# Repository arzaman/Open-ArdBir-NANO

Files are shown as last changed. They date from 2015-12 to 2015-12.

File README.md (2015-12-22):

# Open-ArdBir-NANO
Repository for HW design file (PCB, schematic)  of ArdBir board based on arduino NANO version

Open Ardbir is an open source SW (up to release 2.8.3) to control and automate beer brewing process
The SW have been developed based on Arduino UNO board (Atmega328 MCU) with few surroundings HW component to drive and interface external element (PUMP, Heating element , LCD, push button etc.)

There are few open source HW board available supporting the SW either designed as  shield on top of Arduino Board or stand alone board (all in one board)

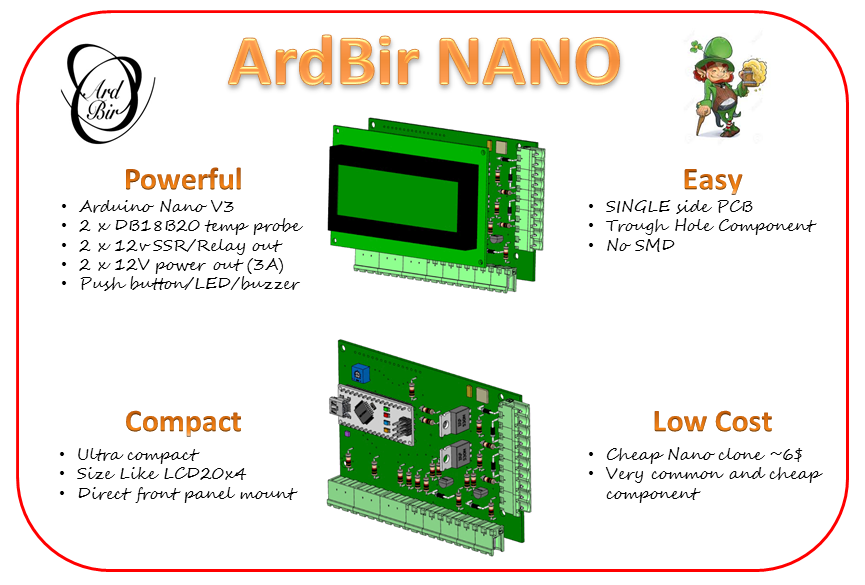
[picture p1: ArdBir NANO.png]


In the repository you can find my personal design of a board based on Arduino NANO V3 version with few additional features (not all supported by current SW version)

•	2 x DB18B20 temp probe

•	2 x 12v SSR/Relay out

•	2 x 12V power out (3A) 

•	Push button/LED/buzzer

The mapping of pinout is completely compatible with all other version (1 x DS18B20,SSR,PUM) while the second set of input is for future applications
The 12V power output can drive directly small pump (like solar project) and/or solenoid valve

The board has been designed in a very compact size to be mounted front panel

•	double side PCB

•	Trough Hole Component

•	No SMD

Two version of PCB are available depending on the LCD mounting

•	LCD solder side: the LCD is mounted on the copper side leaving the components accessible

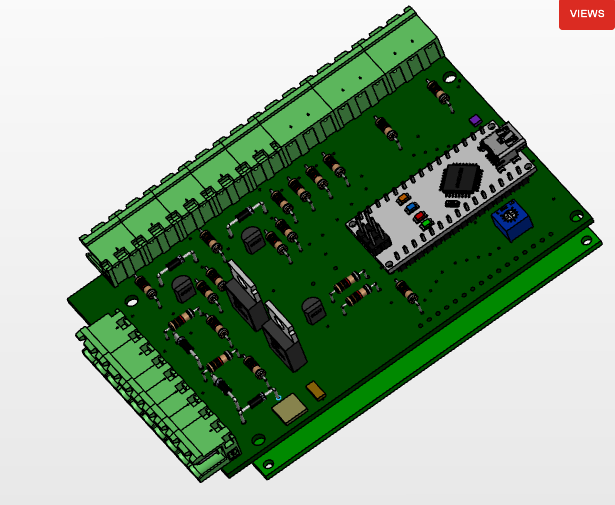
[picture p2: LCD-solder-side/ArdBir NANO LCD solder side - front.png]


•	LCD on component side : LCD is mounted on the same side of components 

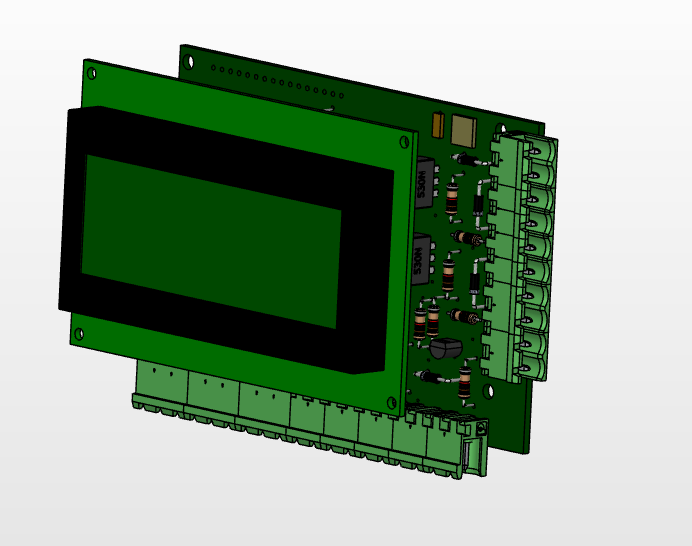
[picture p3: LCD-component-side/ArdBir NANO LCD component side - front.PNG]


In the repository you can find two folders, one for each version, containing PCB and schematic in eagle forma and BoM

![Alt text] (https://github.com/arzaman/Open-ArdBir-NANO/blob/master/LCD-solder-side/ArdBir%20NANO%20schematic.png)

Enjoy and feel free to modify/fork the project

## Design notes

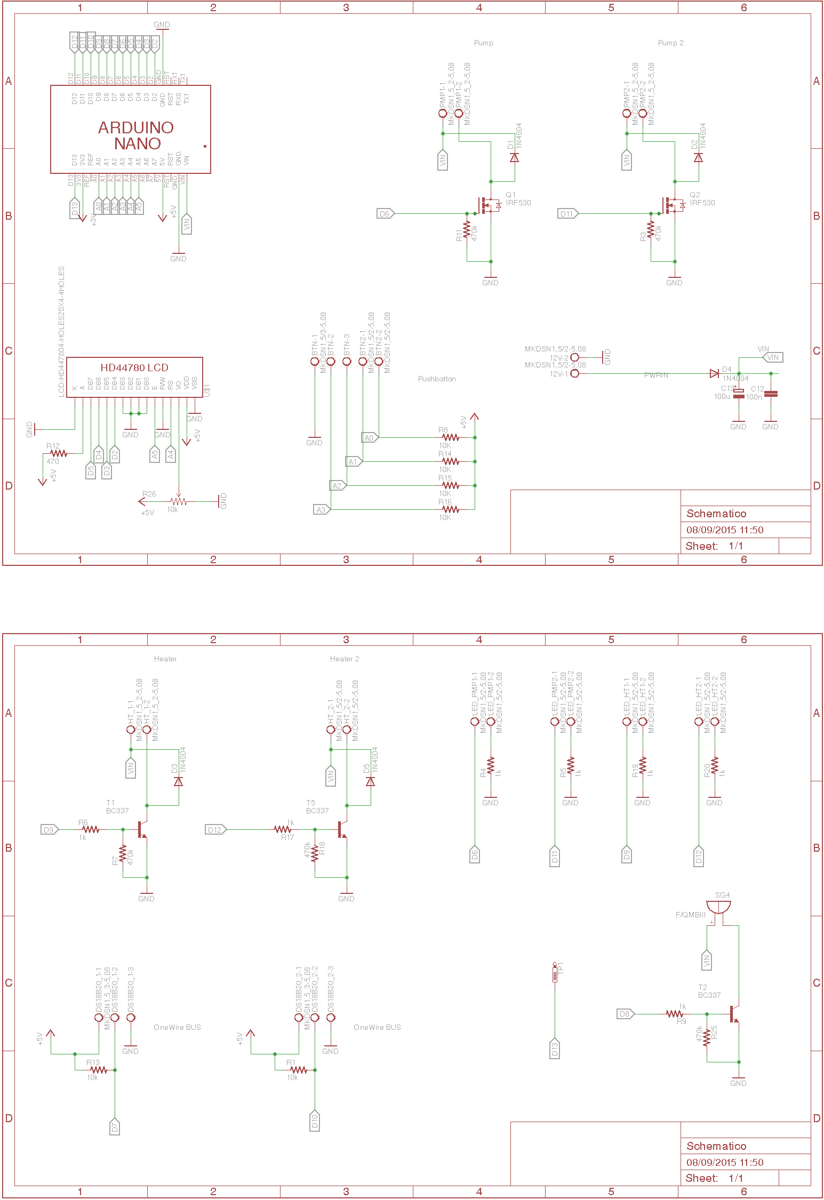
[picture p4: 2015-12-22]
LCD-component-side/ArdBir NANO schematic.png

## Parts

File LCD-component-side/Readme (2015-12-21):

file for the PCB with LCD mounted component side

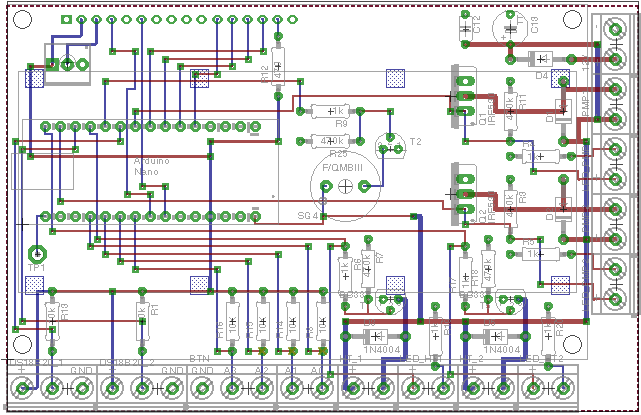
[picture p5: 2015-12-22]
LCD-component-side/ArdBir NANO PCB.png

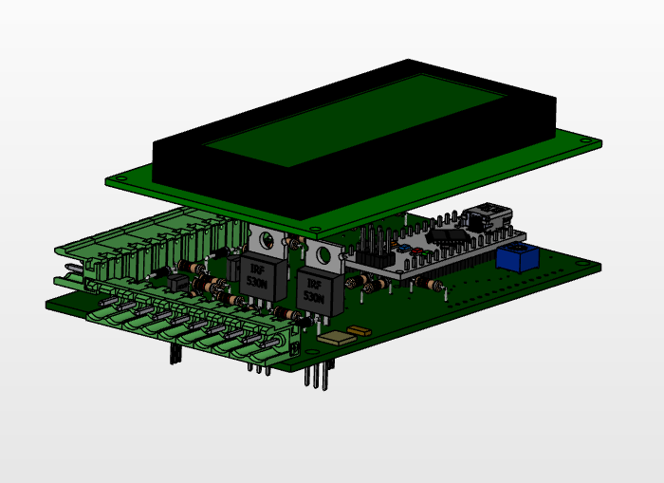
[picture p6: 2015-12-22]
LCD-component-side/ArdBir NANO LCD component side - mid.PNG

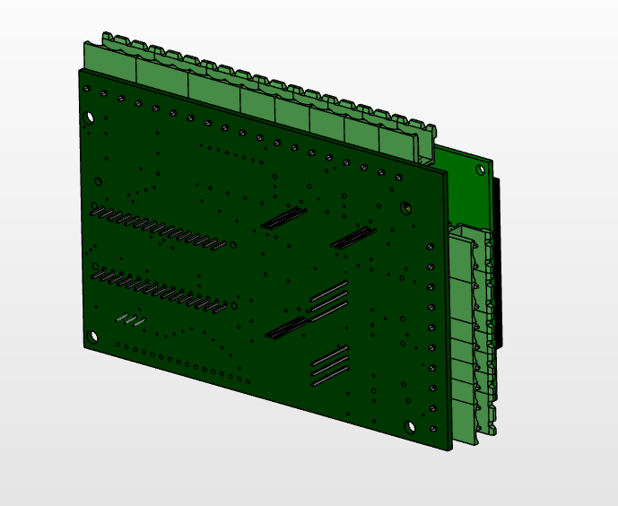
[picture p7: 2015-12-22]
LCD-component-side/ArdBir NANO LCD component side - back.PNG

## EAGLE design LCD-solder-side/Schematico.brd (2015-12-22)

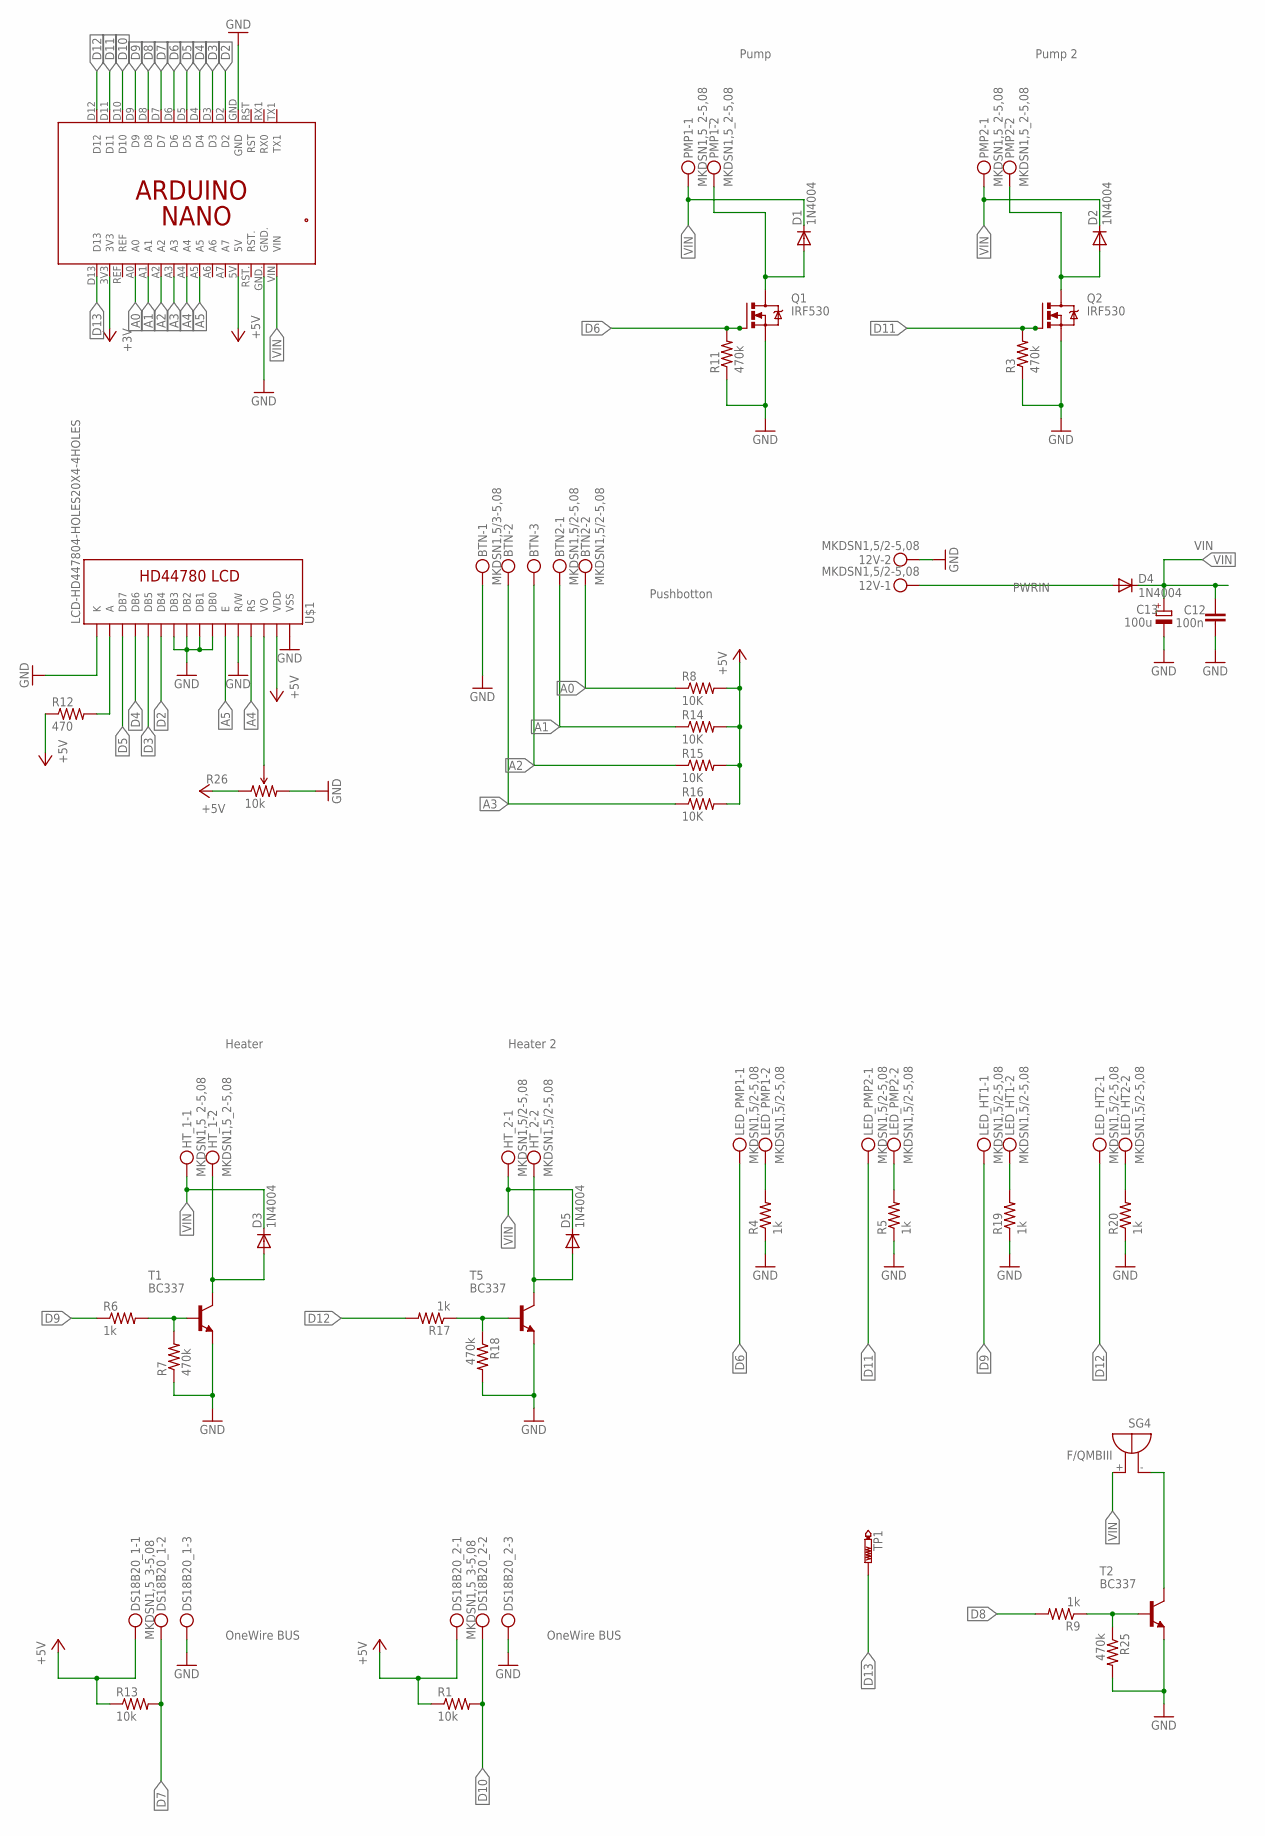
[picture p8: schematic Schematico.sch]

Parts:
12V: MKDSN1,5/2-5,08
BTN: MKDSN1,5/3-5,08
BTN2: MKDSN1,5/2-5,08
C12: 100n; C050-024X044
C13: 100u; TT5D6
D1, D2, D3, D4, D5: 1N4004; DO41-10
DS18B20_1, DS18B20_2: MKDSN1,5_3-5,08; MKDSN1,5-3-5,08
HT_1: MKDSN1,5_2-5,08; MKDSN1,5-2-5,08
HT_2: MKDSN1,5/2-5,08
LED_HT1, LED_HT2: MKDSN1,5/2-5,08
LED_PMP1, LED_PMP2: MKDSN1,5/2-5,08
PCB1: ARDUINO_NANO
PMP1, PMP2: MKDSN1,5_2-5,08; MKDSN1,5-2-5,08
Q1, Q2: IRF530; TO220BV
R1, R13: 10k; 0207/10
R3, R7, R11, R18, R25: 470k; 0207/10
R4, R5, R6, R9, R17, R19, R20: 1k; 0207/10
R8, R14, R15, R16: 10K; 0207/10
R12: 470; 0207/10
R26: 10k; 3362U-2
SG4: F/QMBIII
T1, T2, T5: BC337; TO92
TP1: PTR1PAD1-20; P1-20
U$1: LCD-HD447804-HOLES20X4-4HOLES; LCD-20X4-4HOLES

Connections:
+3V: PCB1.3V3
+5V: DS18B20_1.1, DS18B20_2.1, PCB1.5V, R1.1, R8.2, R12.1, R13.1, R14.2, R15.2, R16.2, R26.1 (CCW), U$1.P$2 (VDD)
A0: BTN2.2, PCB1.A0, R8.1
A1: BTN2.1, PCB1.A1, R14.1
A2: BTN.3, PCB1.A2, R15.1
A3: BTN.2, PCB1.A3, R16.1
A4: PCB1.A4, U$1.P$4 (RS)
A5: PCB1.A5, U$1.P$6 (E)
D2: PCB1.D2, U$1.P$11 (DB4)
D3: PCB1.D3, U$1.P$12 (DB5)
D4: PCB1.D4, U$1.P$13 (DB6)
D5: PCB1.D5, U$1.P$14 (DB7)
D6: LED_PMP1.1, PCB1.D6, Q1.G, R11.2
D7: DS18B20_1.2, PCB1.D7, R13.2
D8: PCB1.D8, R9.2
D9: LED_HT1.1, PCB1.D9, R6.1
D10: DS18B20_2.2, PCB1.D10, R1.2
D11: LED_PMP2.1, PCB1.D11, Q2.G, R3.2
D12: LED_HT2.1, PCB1.D12, R17.2
D13: PCB1.D13, TP1.TP
GND: 12V.2, BTN.1, C12.1, C13.-, DS18B20_1.3, DS18B20_2.3, PCB1.GND, PCB1.GND., Q1.S, Q2.S, R3.1, R4.1, R5.1, R7.1, R11.1, R18.2, R19.1, R20.1, R25.2, R26.3 (CW), T1.1 (E), T2.1 (E), T5.1 (E), U$1.P$1 (VSS), U$1.P$5 (R/W), U$1.P$7 (DB0), U$1.P$8 (DB1), U$1.P$9 (DB2), U$1.P$10 (DB3), U$1.P$16 (K)
unnamed: D2.A, PMP2.2, Q2.D
unnamed: LED_PMP1.2, R4.2
unnamed: LED_PMP2.2, R5.2
unnamed: D1.A, PMP1.2, Q1.D
unnamed: SG4.- (+), T2.3 (C)
unnamed: R9.1, R25.1, T2.2 (B)
unnamed: R12.2, U$1.P$15 (A)
unnamed: D3.A, HT_1.2, T1.3 (C)
unnamed: R26.2 (WIPER), U$1.P$3 (VO)
unnamed: R6.2, R7.2, T1.2 (B)
unnamed: D5.A, HT_2.2, T5.3 (C)
unnamed: R17.1, R18.1, T5.2 (B)
unnamed: LED_HT1.2, R19.2
unnamed: LED_HT2.2, R20.2
PWRIN: 12V.1, D4.A
VIN: C12.2, C13.+, D1.C, D2.C, D3.C, D4.C, D5.C, HT_1.1, HT_2.1, PCB1.VIN, PMP1.1, PMP2.1, SG4.+ (-)

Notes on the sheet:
OneWire BUS
Pump
Pump 2
Heater
Pushbotton
Heater 2

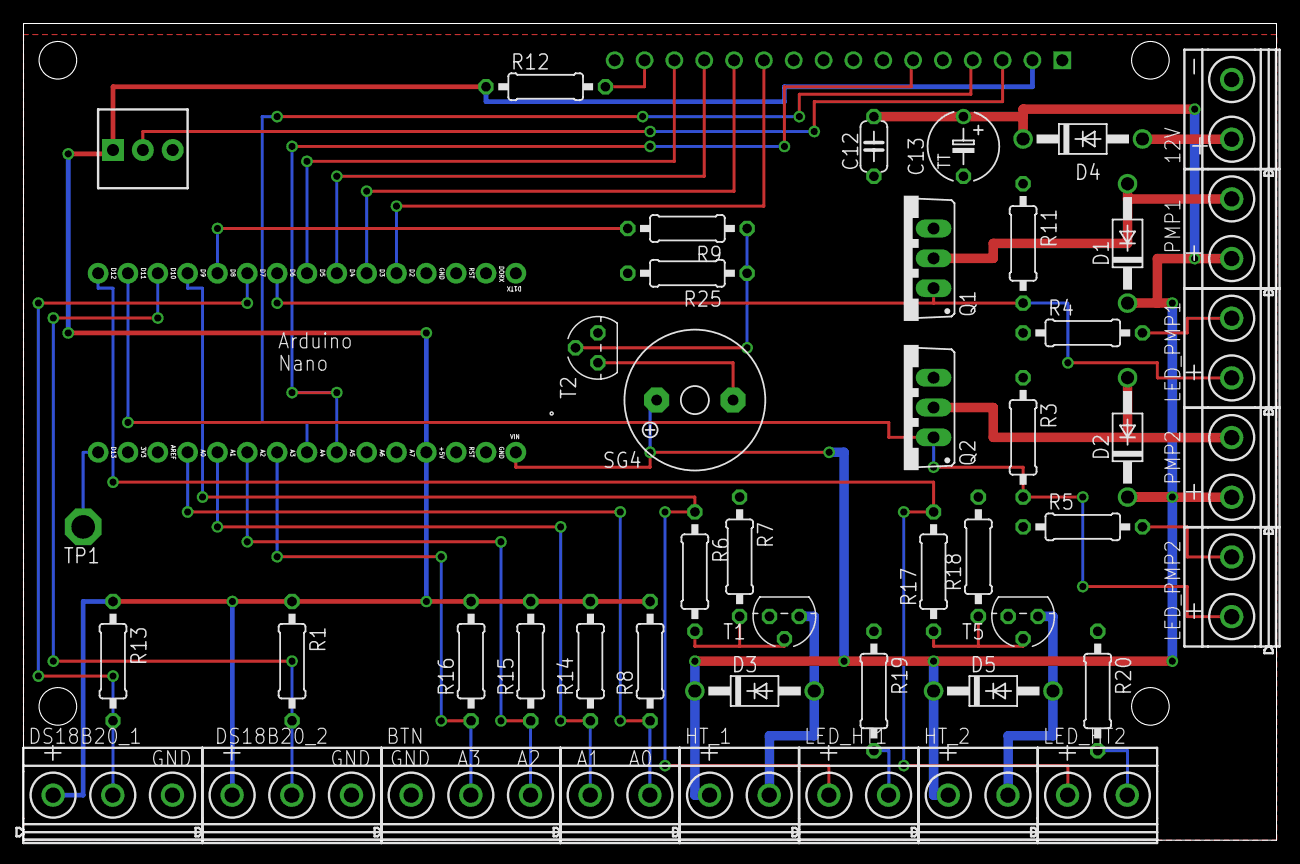
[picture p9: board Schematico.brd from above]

Board: 2 copper layers, 106.7 x 69.5 mm, 49 parts (1 on the bottom side), 36 nets.

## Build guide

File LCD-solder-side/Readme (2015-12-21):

File for the PCB version with LCD mounted copper side

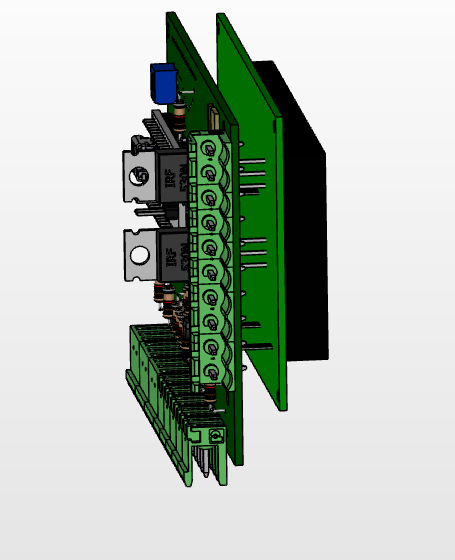
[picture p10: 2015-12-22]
LCD-solder-side/ArdBir NANO LCD solder side - mid.png

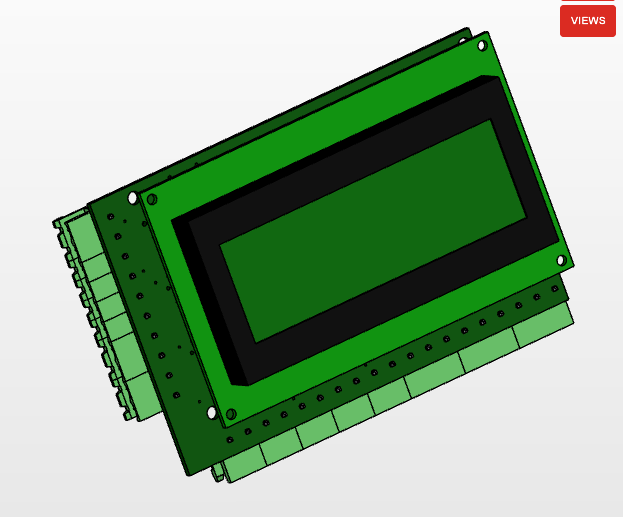
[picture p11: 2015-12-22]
LCD-solder-side/ArdBir NANO LCD solder side - back.png

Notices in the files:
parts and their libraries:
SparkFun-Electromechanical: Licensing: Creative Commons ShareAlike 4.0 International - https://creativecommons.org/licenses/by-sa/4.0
